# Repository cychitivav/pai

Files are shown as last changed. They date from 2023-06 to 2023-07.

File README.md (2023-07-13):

<!--
MARKDOWN IMAGES & BADGES
* https://www.markdownguide.org/basic-syntax/#reference-style-links
* https://github.com/Ileriayo/markdown-badges

EMOJIS
* https://gist.github.com/rxaviers/7360908
  
Find and replace the following text with the name of the project:
	pai
-->

<div align="center" id="readme-top">



<!-- omit in toc -->
# PAI's project
Code and documentation for a UGV that can work and be teleoperated in a field.

[**Explore the docs »**](https://cychitivav.github.io/pai)

[View Demo](https://github.com/cychitivav/pai) · [Report Bug](https://github.com/cychitivav/pai/issues) · [Request Feature](https://github.com/cychitivav/pai/issues)







</div>

<!-- TABLE OF CONTENTS -->
<!-- omit in toc -->
## :pencil:Table of contents
- [:pushpin:About The Project](#pushpinabout-the-project)
	- [Built With](#built-with)
- [:checkered\_flag:Getting Started](#checkered_flaggetting-started)
	- [Prerequisites](#prerequisites)
	- [Installation](#installation)
	- [GitHub Codespace](#github-codespace)
- [:balloon:Usage](#balloonusage)
- [:key:License](#keylicense)
- [:pencil2:Authors](#pencil2authors)
- [:tada:Acknowledgments](#tadaacknowledgments)

<!-- ABOUT THE PROJECT -->
## :pushpin:About The Project

<div align="center">
	<a href="https://cad.onshape.com/documents/2c5667e2c198d5de4bff6632/w/6e55e179f397483a4657fa47/e/d5c2a6fd63cf397246fd908f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">
		
	</a>
</div>

Welcome to the PAI ROS 1 package repository! This package contains source code and documentation for a UGV that can work in a field. This project is part of the *PAI* subject at the Universidad Nacional de Colombia.

> __Note__: This package is being developed using ROS noetic 

<!-- BADGES
https://github.com/Ileriayo/markdown-badges -->
### Built With
* 
* 
* 

<!-- GETTING STARTED -->
## :checkered_flag:Getting Started

This is an example of how you may give instructions on setting up your project locally.
	To get a local copy up and running follow these simple example steps.

### Prerequisites
In order to avoid installing ROS on your local machine, we will be using a docker image to run ROS. So, you will just need to install [Docker](https://docs.docker.com/get-docker/) in your local machine.

### Installation

1. Clone the repo
	```bash
	git clone https://github.com/cychitivav/pai.git
	```
2. Build the docker image
	```bash
	docker build -t pai:latest .
	```
3. Run the docker image
	```bash
	docker run -it \
     		   --rm \
			   -v /tmp/.X11-unix:/tmp/.X11-unix:rw \
               -v $PWD:/root/catkin_ws/src/pai \
			   --name pai \
			   pai:latest
	```
	> __Note__: If you have troubles with the display, try to run the following command before running the docker image:
	> ```bash
	> xhost +local:root
	> ```

### GitHub Codespace
Codespaces add an easy way to start contributing to this project. Some extra step are needed to run the visualization in a remote machine. You need to create a GitHub Codespace:

1. To create a Codespace, click on the following button:
   
	
2. Choose the configuration that best suits you (A high performance configuration is recommended)
3. Wait for the Codespace to be created and set up (It will appear a terminal which is running some scripts)
4. Set a password for the root user
	```bash	
	passwd
	```

From your local machine, you will need to run the following command:

```bash	
gh cs ssh -- -XY
```

> __Note__: You need to have the [GitHub CLI](https://cli.github.com/manual/installation) installed in your local machine.

Then, select the Codespace that you want to connect to and enter the password that you set before.

<!-- USAGE EXAMPLES -->
## :balloon:Usage
In order to run the package, you will need to follow the next steps from the workspace directory (by default, `~\catkin_ws`):

1. Compile packages
```bash
catkin build
```
1. Source the workspace
```bash
source devel/setup.bash
```
1. Launch the package
```bash
roslaunch pai view_robot.launch
```

<!-- ROADMAP -->
<!-- ## :roller_coaster:Roadmap

- [ ] Feature 1
- [ ] Feature 2
    - [ ] Nested Feature

> __Note__: See the [open issues](https://github.com/cychitivav/pai/issues) for a full list of proposed features (and known issues). -->

<!-- CONTRIBUTING -->
<!-- ## :busts_in_silhouette:Contributing

If you have a suggestion that would make this better, please create a pull request.

1. Create your Branch (`git checkout -b <type>/<name>`)
2. Commit your Changes (`git commit -m 'Add some AmazingFeature'`)
3. Push to the Branch (`git push origin <type>/<name>`)
4. Open a Pull Request (in the `git push` response, it appears a link to open a PR) 

The available contribution types are:
* `docs`
* `feat`
* `dev`
* `fix`

Don't forget to give the project a star! Thanks again!
 -->

<!-- LICENSE -->
## :key:License
Distributed under the MIT License. See [`LICENSE`](LICENSE) for more information.

<!-- CONTACT -->
## :pencil2:Authors
* [@cychitivav](https://github.com/cychitivav)
* [@jsduenass](https://github.com/jsduenass)
* [@juvallejom](https://github.com/juvallejom)
* [@Canborda](https://github.com/canborda)
* [@Camilo96A](https://github.com/camilo96a)
* [@jodiazro](https://github.com/jodiazro)

<!-- ACKNOWLEDGMENTS -->
## :tada:Acknowledgments

* Thanks to the [SIMA student group]() who help out supporting this project.

<div align="right">

[:arrow_double_up:back to top](#readme-top)
</div>

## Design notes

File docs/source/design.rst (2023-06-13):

.. _design:
    
Diseño conceptual
#################
Generación de conceptos a partir de análisis funcional y requerimientos
=======================================================================
Alternativas de solución
------------------------
Al momento de buscar alternativas de solución se realizó el boceto de diferentes configuraciones de ruedas, así como mecanismos de transmisión de potencia y sistemas de amortiguamiento  (ver Anexo 400-9 reporte de boceto)

Definición de subsistemas
=========================
Estructura
----------
La estructura está compuesta por placas paralelas atornilladas a los subsistemas de transmisión. De igual forma, la estructura de soporte de interfaz se atornilla a las placas paralelas. Se usa una chapa superior con una matriz de agujeros como interfaz donde se ubican los futuros posibles sensores a usar.

Transmisión y suspensión
------------------------
El sistema de transmisión consta de un eje acoplado al motor, y un elemento de transmisión de torque hacia el acople de la llanta. Este eje irá soportado sobre dos rodamientos que garantizarán la estabilidad estática de este subsistema. También se contará con un mecanismo basculante donde se podrá incorporar una amortiguador para cada una de los subsistemas de transmisión de potencia. 

Potencia eléctrica
------------------
Este sistema está compuesto por un motor eléctrico, una batería y un controlador. El motor eléctrico es el encargado de generar el torque necesario para el movimiento del vehículo. La batería es la encargada de almacenar la energía eléctrica que será suministrada al motor. El controlador es el encargado de regular la energía que es suministrada al motor, de acuerdo a las instrucciones que recibe del sistema de control y comunicación.

Control y comunicación
----------------------
Finalmente, el sistema de control y comunicación está compuesto por una Raspberry Pi, la cual es la encargada de procesar la información recibida por el módulo de comunicación inalámbrica y enviar las instrucciones al sistema de potencia eléctrica.

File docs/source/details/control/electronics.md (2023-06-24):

# Electronics 

## Raspbery pin out 

```{image} https://github.com/cychitivav/pai/assets/30636259/018453a2-3278-494c-a706-0de937c5933a
:alt: Raspberry pin out
:width: 60%
:align: center
```

### Driver left

- FAULT: 35 (GPIO 19)
- PWM2: 31 (GPIO 6) # Back left motor
- PWM1: 19 (GPIO 10) # Front left motor
- DIR2: 13 (GPIO 27)
- DIR1: 11 (GPIO 17)
- EN: 7 (GPIO 4)

### Driver right

- FAULT: 8 (GPIO 14)
- PWM2: 18 (GPIO 23) # Back right motor 
- PWM1: 22 (GPIO 25) # Front right motor
- DIR2: 24 (GPIO 8)
- DIR1: 32 (GPIO 12)
- EN: 40 (GPIO 21)

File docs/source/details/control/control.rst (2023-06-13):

Subsistema de control y comunicaciones
######################################
Selección de unidad de control
==============================
Para la unidad de control encargada de la recepción y procesamiento de datos así como las señales de mando y la transmisión de señales de pwm para el control de los drivers. (Ver anexo 400-15) Donde se tuvieron en cuenta los parámetros de Tensión de Operación, Alimentación, Consumo, Puertos Digitales	Puertos Análogos y Comunicaciones con las que contaba cada tarjeta.

.. toctree::
    electronics

Diseño de conexiones
====================
El subsistema de control y comunicación comprende a diversos elementos electrónicos de control y transmisión. A continuación se listan los componentes vinculados: 
* Raspberry Pi 4
* 2 Drivers Pololu Dual MAX14870 Motor Driver Shield for Arduino
* Regulador de Tensión de 5V a 3A
* Circuito Integrado ATtiny85-20P
* Fusibles y elementos de protección.
* Elementos de conexión : Borneras, interruptores, pines de interconexión.

El diseño electrónico generado se alimenta con la batería de 24V .El subsistema de control se divide en tres secciones independientes.

Alimentación de la tarjeta Raspberry Pi 4.
------------------------------------------
Esta sección está destinada a alimentar la tarjeta Raspberry a partir de la alimentación inicial.  Ya que la tarjeta se alimenta con una tensión de 5V  a una corriente de 3A se requiere incluir un regulador de tensión y demás elementos de protección(fusibles de 3A) para no poner en riesgo la integridad de la tarjeta.

circuito A

Sección Circuito integrado ATtiny 85-20P
----------------------------------------
circuito B

Circuito de control de motores 
------------------------------
Esta sección del montaje eléctrico cuenta con un consumo máximo de 8 amperios, a raíz del consumo de corriente individual de cada uno de los motores.
El circuito parte de una línea de alimentación de 24V y un elemento de activación (interruptor de Parada de Emergencia) el cual interrumpe el funcionamiento del vehículo sin necesidad de apagar el sistema de control en su totalidad, apagando únicamente los motores.
Esta línea alimenta los drivers los cuales controlan 2 motores cada uno. A partir de la tarjeta de control Raspberry se controlan los valores de PWM y Dirección. Ver planos

circuito C

Fabricación de PCB
==================
El diseño electrónico propuesto para el subsistema de control implica un gran número de conexiones, sin embargo no se amerita la fabricación de una Placa de Circuito Impreso de doble cara.
Uno de los factores de  diseño y fabricación de esta placa es la presencia de altas corrientes en ella. Para la capa de cobre trasera (B.Cu) se manejó un grosor estándar de 0.035mm. En función de este espesor y la cantidad de corriente que transita por las pistas se definió el ancho de las mismas generando tres clases : 

+---------------+----------------+----------------------------+-----------------------+
| Tipo de Pista | Ancho de Pista | Factor de Diseño           | Aplicaciones          |
+===============+================+============================+=======================+
| Pista A       | 0.4 mm         | Baja corriente. Caminos que| Conexiones entre el   |
|               |                | no requieren ningún tipo de| circuito integrado,   |
|               |                | limitación en corriente. Se| la tarjeta Raspberry y|
|               |                | escoge este espesor por    | los controladores.    |
|               |                | viabilidad de las          |                       |
|               |                | conexiones a raíz de un    |                       |
|               |                | proceso de iteración en el |                       |
|               |                | diseño.                    |                       |
+---------------+----------------+----------------------------+-----------------------+
| Pista B       | 1.27 mm        | Pistas con una corriente   | Conexiones de potencia| 
|               |                | admisible de 3 A.          | para la tarjeta       |
|               |                |                            | Raspberry.            |
+---------------+----------------+----------------------------+-----------------------+
| Pista C       | 2.54 mm        | Pistas con una corriente   | Alimentacion de       |
|               |                | admisible de 8 A           | Controladores y       |
|               |                |                            | motores.              |
+---------------+----------------+----------------------------+-----------------------+

A continuación se presenta una imagen del diseño final para la Placa de Circuito Impreso vinculada al sistema de control.

PCB

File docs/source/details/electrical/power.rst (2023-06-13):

Subsistema de potencia eléctrica
================================

Selección de motores
--------------------
.. toctree::
    motor

Selección de controladores de motor
-----------------------------------
Para la implementación de los motores DC seleccionados es necesario incluir un controlador de motor o Driver con el fin de modificar la señal de control adaptándola para que esta esté en la capacidad de inducir movimiento en el motor. 

Para dicha selección se tuvieron en cuenta cinco parámetros principales enumerados a continuación : 
* **Tensión o Voltaje de operación [V]:** Se seleccionan drivers cuyo voltaje de alimentación sea superior al voltaje del motor. Por generalidad, se opta por tensiones de alimentación esté entre 1,5 y 2 veces el voltaje del motor.
* **Corriente Promedio [A]:**  Parámetro relacionado con la corriente consumida por el controlador. Como criterio de selección para este parámetro ,se definió que su valor mínimo  debe ser la corriente asociada al torque máximo que puede entregar el motor (stall current).
* **Tensión de la señal de control [V]:** Valor de voltaje para la señal de salida del driver. 
* **Frecuencia de PWM [kHz]:** Frecuencia de los pulsos de la señal de control. 
* **Reversibilidad:** Se evalúa la capacidad del controlador de invertir el sentido de giro para el motor seleccionado.

Matriz de decisión para la selección de driver
^^^^^^^^^^^^^^^^^^^^^^^^^^^^^^^^^^^^^^^^^^^^^^

+------------------+----------------------+--------------------+--------------------------------+-------------------+----------------+
|                  | Tensión de operación | Corriente promedio | Tensión de la señal de control | Frecuencia de PWM | Reversibilidad |
+==================+======================+====================+================================+===================+================+
| RioRand Upgraded |                      |                    |                                |                   |                |
| DC Motor Pump    | 6-90 V               |  8-15 A            | 0-5 V                          | 15 kHz            | No             |
| Speed Controller |                      |                    |                                |                   |                |
| 6-90 V 15A       |                      |                    |                                |                   |                |
+------------------+----------------------+--------------------+--------------------------------+-------------------+----------------+
| RioRand 8-50V DC |                      |                    |                                |                   |                |
| Motor Speed      | 8-50 V               | 20-30 V            | 0-5 V                          | 12 kHz            | No             |
| Controller       |                      |                    |                                |                   |                |
| for Power Wheel  |                      |                    |                                |                   |                |
| PWM Switch       |                      |                    |                                |                   |                |
+------------------+----------------------+--------------------+--------------------------------+-------------------+----------------+
| RioRand 6V 12V   |                      |                    |                                |                   |                |
| 24V 28V 3A 80W   | 6-28 V               | 3A                 | 0-5 V                          | 10 kHz            | Si             |
| DC Motor Speed   |                      |                    |                                |                   |                |
| Controller       |                      |                    |                                |                   |                |
+------------------+----------------------+--------------------+--------------------------------+-------------------+----------------+
| Pololu Dual      |                      |                    |                                |                   |                |
| MAX14870 Motor   | 4,5 - 36 V           | 1,7 A              | 0-5V                           | 50 kHz            | Si             |
| Driver Shield    |                      |                    |                                |                   |                |
| for Arduino      |                      |                    |                                |                   |                |
+------------------+----------------------+--------------------+--------------------------------+-------------------+----------------+

Selección de batería
--------------------
Para la selección de la batería se establecieron los siguientes parámetros a tener en cuenta:

* **Voltaje de la batería [V]:** parámetro dependiente del tipo de motor seleccionado.
* **Capacidad de almacenamiento [mAh]:** 
* **Corriente entregada [mA]:** Parámetro relacionado con la capacidad de descarga [C] de la batería. 
* **Costo estimado [$]:** una estimación inicial de  300 mil pesos
* **Tamaño [mxmxm]:** Dependiente del tamaño de chasis 
* **Peso:** Búsqueda de reducción de peso
* **Densidad energética [Wh/kg]:**
* **Disponibilidad:** Facilidad de encontrar la batería en el comercio local.

Se realizó una búsqueda de los tipos de baterías existentes haciendo énfasis en encontrar las baterías que se utilizan en aplicaciones adyacentes, es decir baterías para vehículos eléctricos  como por ejemplo baterías usadas en bicicletas eléctricas.  Se obtuvieron como resultado  los siguientes tipos Plomo, Gel, Li-Ion, LiFePo4, LiPo, Ni-Mh, Ni-Cd. Sobre los cuales se descartaron las de Ni-Mh, Ni-Cd y gel debido a no cumplir la restricción de disponibilidad y no haber elementos asequibles en el mercado local.
Sobre las restantes se realizó una evaluación calificando su idoneidad en una una escala de 1 a 5 respecto a los parámetros de selección restante. 

+------------------+---------------------+------------------------+--------------------------+---------------------+
|                  | Plomo               | Li-Ion                 | LiFePo4                  | LiPo                |
+==================+=====================+========================+==========================+=====================+
| Voltaje          | 3                   | 5                      | 5                        | 4                   |
| de la batería    |                     |                        |                          |                     |
+------------------+---------------------+------------------------+--------------------------+---------------------+
| Debe tener un    | Batería a 12 voltios| El paquete modular     | Versión de batería a 12, | Versión a 21.5 o    |
| voltaje de hasta | Necesidad de comprar| permite establecer     | 24 y 48 V                | 25.7 V              |
| 24 V.            | 2 baterías para     | el voltaje por número  |                          |                     |
|                  | cumplir requisito.  | de baterías en serie   |                          |                     |
+------------------+---------------------+------------------------+--------------------------+---------------------+
| Capacidad de     | 5                   | 4                      | 4                        | 3                   |
| almacenamiento   |                     |                        |                          |                     |
+------------------+---------------------+------------------------+--------------------------+---------------------+
| Define la        | 7.5 Ah              | 7.8 Ah batería 6S3P    |                          |                     |
| autonomía del    |                     |                        |                          |                     |
| robot            |                     |                        |                          |                     |
+------------------+---------------------+------------------------+--------------------------+---------------------+
| Corriente        | 2                   | 4                      | 3                        | 3                   |
| entregada        |                     |                        |                          |                     |
+------------------+---------------------+------------------------+--------------------------+---------------------+
| Costo            | 3                   | 4                      | 3                        | 3                   |
+------------------+---------------------+------------------------+--------------------------+---------------------+
| Tamaño           | 2                   | 4                      | 2                        | 4                   |
+------------------+---------------------+------------------------+--------------------------+---------------------+
| Peso             | 2                   | 4                      | 2                        | 3                   |
+------------------+---------------------+------------------------+--------------------------+---------------------+
| Densidad         | 3                   | 3                      | 3                        | 5                   |
| energética       |                     |                        |                          |                     |
+------------------+---------------------+------------------------+--------------------------+---------------------+
| **Acumulado**    | **12**              | **28**                 | **23**                   | **26**              |
+------------------+---------------------+------------------------+--------------------------+---------------------+

Donde a partir de la evaluación se decidió escoger una batería ion litio de configuración 6S3P

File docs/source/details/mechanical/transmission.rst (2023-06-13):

Subsistema de transmisión
=========================
Selección de rodamientos
------------------------
Para llevar a cabo esta evaluación, se recopilaron los datos técnicos proporcionados por SKF y se compararon con los requisitos de carga especificados. Además, se consideraron aspectos como la capacidad de carga, las dimensiones del rodamiento, la calidad y confiabilidad del fabricante, así como la lubricación.

Resultados:
^^^^^^^^^^^

* **Capacidad de carga:** Según la información suministrada por SKF, el rodamiento 63003 tiene una capacidad de carga radial estática de 3,25 kN y una capacidad de carga radial dinámica de 6,56 kN. Dado que la carga radial en la aplicación es de 500 N, se determinó que el rodamiento seleccionado puede soportar de manera segura esta carga con un margen significativo.
* **Dimensiones:** El rodamiento 63003 SKF tiene un diámetro interior de 17 mm, un diámetro exterior de 35 mm y un ancho de 14 mm. Estas dimensiones son adecuadas para la aplicación en consideración, lo que permite un ajuste adecuado y un funcionamiento eficiente.
* **Calidad y confiabilidad:** SKF es reconocido como un fabricante líder en la industria de rodamientos, conocido por producir productos de alta calidad y confiables. Esto respalda la fiabilidad del rodamiento 63003 SKF y su capacidad para resistir condiciones exigentes en la aplicación.
* **Lubricación:** El rodamiento 63003 SKF se suministra prelubricado de fábrica con grasa de alta calidad. Esto reduce la fricción y el desgaste, y contribuye a una vida útil prolongada del rodamiento. Sin embargo, se recomienda mantener una adecuada lubricación durante la operación para garantizar un rendimiento óptimo a largo plazo.

En conclusión, con base en los resultados del análisis, se concluye que el rodamiento 63003 SKF es una elección adecuada para soportar cargas radiales de 500 N en la aplicación estudiada. Su capacidad de carga, dimensiones apropiadas, calidad y confiabilidad, respaldadas por la reputación del fabricante, lo convierten en una opción recomendada.

Diseño del eje y elementos auxiliares
-------------------------------------
El dimensionamiento del eje involucra varias iteraciones de diseño, donde se analizaron las distintas implicaciones que conllevaba cada geometría del eje. Inicialmente se optó por la geometría dispuesta en la figura del eje, donde se cuenta con 3 secciones de diámetros diferentes. La sección externa tendría un diámetro de 34.1 milímetros con el fin de encajar en la flor que acopla la llanta., mientras una sección central de mayor diámetro permitiría durante el progreso del diseño impedir el deslizamiento axial de este eje. El diámetro más interno corresponde a las dimensiones de los rodamientos seleccionados. Dentro de esta sección se maquinaría un agujero con chavetero que permitiría la transmisión de torque del motor a este eje. La dimensión de esta abertura estaría predefinida por las dimensiones del eje de salida del motor ya escogido. Por otro lado durante la primera iteración se establecieron las fuerzas que actuaban sobre el eje, que eran producidas por el resto de elementos en contacto con este(Rodamientos, acople llanta, eje del motor), las cuales también se encuentran en la siguiente figura.

eje1

Al considerar todas estas interacciones se llegó a un sistema estáticamente indeterminado que sería difícil de complementar con una ecuación de deformación, debido a las diferentes y complejas geometrías preliminares. Si se asume que el motor es totalmente soportado por la estructura externa, entonces este no ejercería una fuerza radial sobre el eje, solamente ejercería el torque, por lo que se para las siguientes iteraciones se despreciaría esta fuerza (E1). Durante el estudio de distribución de fuerzas sobre el eje se consideraron varios valores para s y L, y se observó que L afecta enormemente el momento flector que siente el eje, por lo que se opta por mantener esta distancia lo mínima posible. También se elige mantener la distancia entre los rodamientos de apoyo en aproximadamente 30 milímetros, con el fin de minimizar el momento a la vez que se deja espacio para el mecanismo basculante que va sobre la estructura auxiliar. 

Posteriormente se observó que el cambio de diámetro de 34 mm a 17 mm causaba un importante concentrador de esfuerzos, lo que hizo reconsiderar todo el diseño del eje. Es de esta manera que se decidió utilizar un diámetro único de 17 mm para todo el eje y de esta manera evitar los concentradores de esfuerzos por cambios abruptos de sección, para acoplar la flor de la llanta al eje se opta por usar una camisa auxiliar que permita encajar el eje y la flor de la llanta a su vez que mantiene la transición centrada. Debido a la sección única, se decidió utilizar anillos seeger para evitar el deslizamiento axial del eje. Estos anillos se situarían en unas ranuras que van en el espacio entre los dos rodamientos de apoyo. Además para transmitir el torque a la llanta se opta por usar un pasador que atraviesa la flor, la camisa y el eje como tal, por lo que se hace necesario maquinar en el eje un agujero transversal donde vaya alojado este pasador de transmisión. Es así que se llega al nuevo y definitivo diseño del eje, que se puede observar en la siguiente figura. 

eje1

Para verificar el correcto diseño de este eje se lleva a cabo un detallado análisis que permite establecer el factor de seguridad a fatiga del eje junto a los componentes auxiliares de este (Camisa y pasador). Dicho análisis puede verse en el anexo “Diseño de elementos de transmisión de potencia”. En dicho análisis se observó que se puede optimizar el factor de seguridad en función del diámetro del pasador. De este análisis se obtuvo un factor de seguridad mínimo y óptimo de aproximadamente 1.8, que corresponde a la fatiga por flexión del pasador. Ya con dicho factor se dan por establecidas todas las dimensiones del eje, camisa y pasador.

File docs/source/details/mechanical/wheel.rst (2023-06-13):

Selección de las ruedas
#######################

En el proceso de selección de las ruedas para nuestro vehículo teleoperado, consideramos diferentes aspectos para encontrar la mejor opción. Nuestro enfoque principal fue la aplicación específica del vehículo y la disponibilidad de las ruedas en el mercado.

Inicialmente, consideramos utilizar ruedas de cuatrimoto con un diámetro de rin de 6 pulgadas. Específicamente, evaluamos las ruedas *Hakuba* que presentaban un labrado de aproximadamente 1 cm, lo cual las hacía adecuadas para enfrentar los desafíos del terreno en el que operaría el vehículo.

Ruedas costosas

Sin embargo, al evaluar los costos asociados y los requisitos de diseño adicionales, decidimos descartar esta opción. El costo de estas ruedas de cuatrimoto ascendía a 1 millón de pesos, sin contar el gasto adicional de diseñar un acople para unirlas al motor del vehículo.

Posteriormente, nos dirigimos al mercado de ruedas y rodachinas en el sector de Ricaurte para buscar alternativas más económicas. Allí encontramos unas ruedas de 10 pulgadas de diámetro que incluían el rin y el acople necesario, a un costo de 50 mil pesos. Estas ruedas estaban diseñadas específicamente para plataformas de carga de hasta 200 libras, lo cual las convertía en una opción ideal para nuestro vehículo teleoperado de muestreo de suelos. Además, si el labrado no fuese suficiente para enfrentar el terreno, podríamos cambiar la llanta por una de mayor agarre, sin necesidad de cambiar el rin o el acople, esto claro, con consentimiento del cliente.

Ruedas económicas

La selección de las ruedas de 10 pulgadas nos brindó una solución más rentable, ya que cumplía con nuestros requisitos de tracción y estabilidad a un precio mucho más accesible. Además, el hecho de que estas ruedas ya incluyeran el acople necesario simplificó el proceso de integración en el vehículo, ahorrando tiempo y esfuerzo en el diseño y fabricación de un acople adicional.

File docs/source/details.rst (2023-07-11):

.. _detail:

Generación detallada del producto
#################################
Basándonos en la experiencia de expertos y diversas fuentes consultadas, se ha determinado que el diseño de cualquier vehículo debe realizarse de las ruedas hacia arriba. Esto se debe a que los componentes ubicados en la parte inferior del vehículo definen características y requisitos para los componentes superiores.

El diseño del vehículo teleoperado se inicia centrándose en las ruedas, ya que desempeñan un papel fundamental al soportar la carga, proporcionar tracción y determinar la capacidad de movimiento en el terreno. 

A medida que avanzamos en el proceso de diseño, se analizaron y definieron cuatro subsistemas principales: estructural, transmisión, potencia eléctrica y control y comunicaciones. Esto debido a que a pesar que el vehículo cuenta con cuatro ruedas, el sistema de tracción se va a comportar como un vehículo diferencial, es decir, que las ruedas del lado izquierdo y derecho se moverán de forma independiente.

.. toctree::
    :maxdepth: 2

    details/mechanical/wheel
    details/mechanical/structural
    details/mechanical/transmission
    details/electrical/power
    details/control/control
    details/control/electronics
    details/control/software_setup

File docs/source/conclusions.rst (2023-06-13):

Conclusiones y trabajo futuro
#############################
Conclusiones
============
* El prototipo desarrollado comprende una primera aproximación a la automatización de muestreo de suelos. Si bien aún se requiere de un operario que manipule el vehículo, el recorrido de este permitirá la captura de datos georreferenciados con una resolución superior a la obtenida por las técnicas tradicionales y menor tiempo requerido en campo.
* Si bien el prototipo puede no funcionar bien en algunos terrenos con pendiente o con tamaño de agregado demasiado grande, en ambientes controlados su desempeño ha sido sobresaliente.
* El diseño conceptual depende de la disponibilidad comercial de algunas piezas, esto facilita su mantenimiento y reparación en caso de ser necesario reemplazar componentes dañados o desgastados.
* El presupuesto ajustado limitó la adquisición de algunos componentes de mayor calidad o precisión que posiblemente habrían resultado en un incremento en el desempeño del prototipo final.

Trabajo futuro
==============

Autonomía del robot
-------------------
El alcance del presente proyecto limitó el prototipo a ser teleoperado, de manera que el sistema de control funciona en lazo abierto y la única realimentación de la localización del vehículo es la observación directa del operario. Se espera a futuro seguir trabajando dentro del semillero SIMA en la implementación de sensores que permitan al robot solucionar el problema de navegación y generar trayectorias de forma independiente.

Suspensión
----------
Si bien el diseño de detalle presenta un sistema de amortiguamiento, este no pudo ser implementado en la construcción del prototipo debido a problemas de disponibilidad de los componentes. Se espera en un futuro adquirir los resortes que cumplan con las especificaciones calculadas e instalarlos en el prototipo.

Captura de datos
----------------
El subsistema de captura de datos georreferenciados no estaba contemplado en el presente proyecto, sin embargo comprende la aplicación real del vehículo desarrollado. El objetivo del semillero es proponer un nuevo proyecto para diseñar y/o adecuar sensores que permitan la medición de variables físicas del suelo e implementar (en lo posible en el mismo controlador) un software que almacene estas mediciones para futuro procesamiento.

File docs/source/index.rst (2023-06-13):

Vehículo de Muestreo
####################

Este informe presenta el diseño y desarrollo de un vehículo de muestreo en aplicaciones agrícolas, diseñado para facilitar la recolección eficiente y precisa de muestras de suelo en áreas no perturbadas. El vehículo fue concebido como parte de un proyecto de la materia Proyecto Aplicado de Ingeniería en la Universidad Nacional de Colombia. El proyecto fue desarrollado por un equipo de 7 estudiantes de ingeniería mecánica y mecatrónica, bajo la supervisión de un profesor de la facultad de ingeniería.

En el presente informe, se describirán los pasos clave seguidos en el proceso de diseño y construcción del vehículo, así como las pruebas y validaciones realizadas para evaluar su desempeño y funcionalidad. También se incluirán los detalles técnicos relevantes, como las especificaciones del vehículo, los componentes utilizados y los procedimientos de operación.

Esperamos que este informe sirva como una guía útil para aquellos interesados en el diseño y construcción de vehículos similares, y que fomente futuras investigaciones y desarrollos en este campo de estudio. Agradecemos cualquier comentario o sugerencia que pueda contribuir a mejorar el diseño y funcionalidad del vehículo en futuras iteraciones.

.. toctree::
   :maxdepth: 3
   :caption: Tabla de contenido
   :numbered:

   problem
   metodology
   design
   details
   verification
   manufacturing
   validation
   conclusions

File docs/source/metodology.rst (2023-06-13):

Metodología del proyecto
########################
Para el presente proyecto se optó por una metodología en cascada ya que sus etapas debían desarrollarse de manera secuencial y el alcance está limitado a una sola iteración (tanto por recursos económicos como temporales), que consiste en la construcción de un primer prototipo como producto final. Las subsecciones siguientes describen las etapas seguidas y las actividades para cada una.

Etapa de análisis de requisitos
===============================
En esta etapa se recopilaron los requisitos del proyecto con base en las necesidades del cliente y a partir de investigación y asesoría por parte de expertos. Las principales actividades desarrolladas se describen a continuación.

Investigación del estado del arte
---------------------------------
Se realizó una investigación detallada de los diferentes robots móviles con aplicaciones en agricultura (como se ha descrito brevemente en la sección :ref:`art`) desde dos perspectivas; modelos que se consiguen comercialmente y prototipos desarrollados en un ambiente más académico e investigativo. Esta contextualización permitió comprender las especificaciones y requerimientos de ingeniería, y una vez comprendidos los parámetros se comenzaron a proponer ideas de diseño a partir de diferentes técnicas de trabajo grupal como lluvia de ideas.

Asesoría de expertos
--------------------
Con el fin de comprender a profundidad el proceso de diseño y los parámetros requeridos para la construcción de un robot con las características solicitadas, se buscó asesoría en diferentes personas con conocimiento y experiencia en el área de la robótica móvil y de la tecnificación de la agricultura. El ingeniero Carlos Velázquez (AmiTech), a partir de su experiencia trabajando con robots móviles, dio recomendaciones sobre diferentes modelos que se podían usar como base y tipos de transmisión, también hizo comentarios sobre el nivel de autonomía que puede tener el robot móvil en relación con su complejidad, y sobre alternativas de alimentación para el sistema eléctrico. Por otra parte, el ingeniero Luis David Ordoñez es docente del curso de Electrotecnia impartido para el programa de Ingeniería Agrícola y ha trabajado con UAV y UGV en labores agrícolas, y su asesoría se enfocó principalmente en cómo solucionar el problema de tracción y navegación del vehículo junto con la adquisición de datos georreferenciados (subsistema fuera del alcance del presente proyecto). Finalmente, el ingeniero Felipe González ex docente de la asignatura de Robótica, realizó aportes sobre el modelo cinemático para un robot móvil tipo diferencial.

Reuniones con cliente
---------------------
Otra actividad recurrente en esta etapa fue una serie de reuniones con el cliente y varios miembros del semillero SIMA con el fin de comprender y detallar las necesidades del problema y además obtener retroalimentación sobre las ideas y propuestas que se iban presentando. Los temas discutidos se detallan en las actas.

Etapa de diseño
===============
Una vez establecidos los requisitos se procedió al diseño conceptual y de detalle del producto. Para esta etapa se utilizó la plataforma OnShape que permite el modelado CAD con control de versiones de manera que se pudieran visualizar y probar múltiples conceptos sin afectar el diseño principal. Este diseño comenzó a partir de los bocetos generados en la lluvia de ideas y modelos base obtenidos en la etapa previa del proyecto, posteriormente se definieron los subsistemas y se inició con el diseño de detalle aplicando los conceptos de ingeniería adquiridos a lo largo de la formación académica (la profundización de este proceso se describe en las secciones :ref:`design` y :ref:`detail`). Esta etapa describe un proceso cíclico dentro del diseño, ya que a partir de cálculos previos se diseñan piezas y se seleccionan componentes que posteriormente son simulados o verificados de manera que cumplan teóricamente con los requerimientos, en caso de falla se debe volver a diseñar o cambiar la pieza y retornar a la verificación hasta que todas las partes hayan sido aprobadas.

Etapa de implementación
=======================
Esta etapa comprende la construcción física del vehículo. Para esto se dividió en tres actividades principales; la fabricación de las piezas diseñadas y la adquisición de piezas estandarizadas debían llevarse a cabo de forma paralela, teniendo en cuenta los tiempos de fabricación y de envío según correspondiera, para posteriormente iniciar con el ensamble y puesta a punto del prototipo. Para esta etapa se contó con empresas proveedoras de material industrial, diferentes negocios de mecanizado y corte láser en la ciudad de Bogotá y además se dispuso del Laboratorio de Mecanización en el edificio de Ingeniería Agrícola de la Universidad Nacional de Colombia sede Bogotá para todo el proceso de ensamblado. Más detalle de esta etapa se describe en la sección :ref:`assembly`.

Etapa de pruebas y validación
=============================
Una vez finalizado el ensamble del prototipo, este se someterá a una serie de pruebas que comprueben el correcto funcionamiento de cada uno de los subsistemas que lo comprenden. Estas pruebas deben ser ejecutadas en ambiente controlado y se deberán realizar mediciones de las variables que confirmen que el modelo cumple con los requerimientos de diseño definidos. Las validaciones a realizar se describen en el anexo de protocolos de validación.

Etapa de mantenimiento y soporte
================================
Una vez validado el prototipo al cliente, se hará la entrega formal donde se indiquen las instrucciones de uso, recomendaciones y futuras mejoras, dando así como finalizada la vinculación formal del contrato social. Sin embargo, se ha extendido la invitación a los integrantes del equipo de trabajo para continuar con el proyecto desde el semillero.

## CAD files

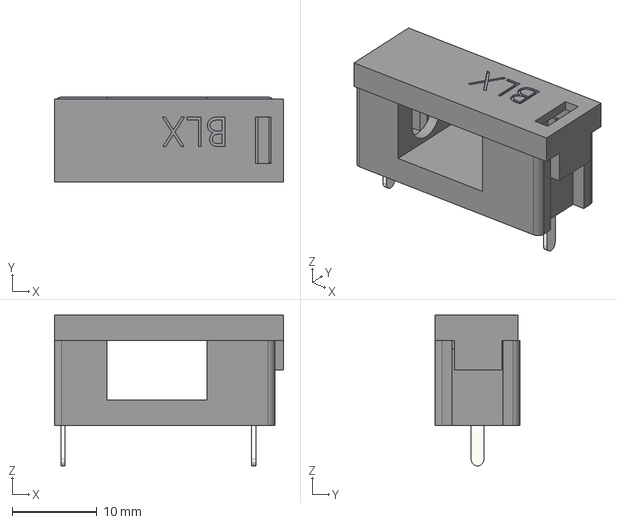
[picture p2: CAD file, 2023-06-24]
kicad/model/Fuse Holder.step
27.0 x 10.0 x 17.8 mm

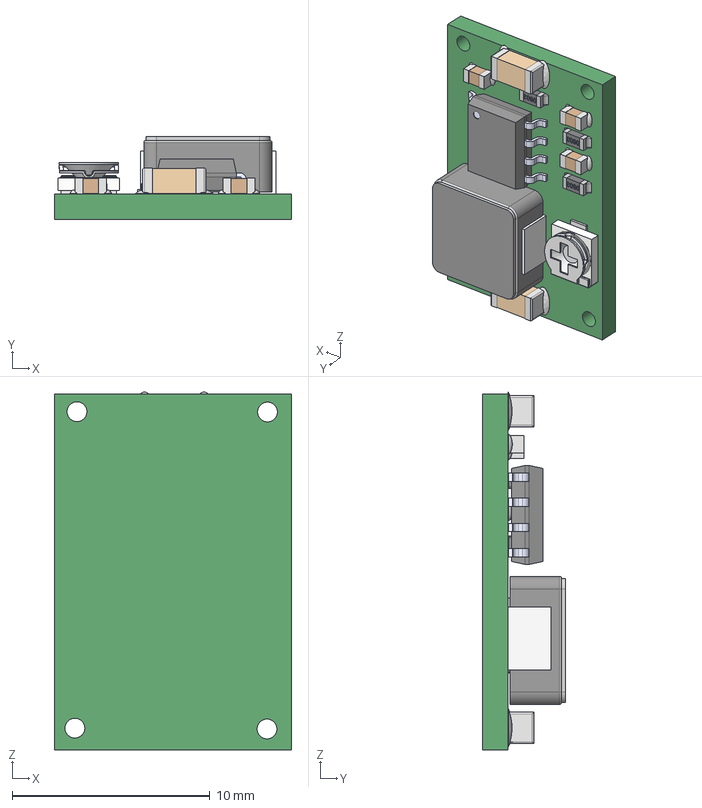
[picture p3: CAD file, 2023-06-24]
kicad/model/dsn-mini-360.step
12.0 x 4.20 x 18.1 mm
User Library-SOIC-8 - TEK
Resistor 0603 x 3
CAPC0603 x 3
CAPC1206 x 2
EVM-3E

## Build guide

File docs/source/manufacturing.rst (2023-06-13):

.. _assembly:

Fabricación y ensamble
######################

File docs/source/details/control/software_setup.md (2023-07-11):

# Raspberry set up

## Install OS
This project is using Ubuntu 20.04 as the base OS. Use the official ubuntu guide and follow step by step installation process. [^os-install]

 > __Note:__ Ubuntu Desktop 2020 is not available in the rpi-imager so Ubuntu Server 2020 is the one used. And the following command is needed to download the necessary package to configure the desktop version.
 > ```
 > sudo apt update
 > sudo apt install ubuntu-desktop
 > ```

## Set up ROS
Follow the ROS installation guide [^ros-install] to install __ROS noetic__.

## Install pigpio lib
Install the pigpio library with the following commands [^pigpio-install].

```bash
apt install unzip
wget https://github.com/joan2937/pigpio/archive/master.zip
unzip master.zip
cd pigpio-master
make
sudo make install
sudo rm -rf master.zip pigpio-master
```

## Get project 
This project is configured as a ROS package. Clone the repo inside your workspace

```bash
mkdir -p ~/catkin_ws/src
cd ~/catkin_ws/src
git clone https://github.com/cychitivav/pai
```

## Build the ROS package

```bash
cd ~/catkin_ws
catkin build
source devel/setup.bash
```
## Run robot

```
roslaunch pai run_robot.launch
```

```
rostopic pub  -r 0.5 /front_right_wheel_ctrl/command std_msgs/Float64 "64.0"
```

```
rostopic pub -r 0.5 /cmd_vel geometry_msgs/Twist "linear:
  x: 1.0
  y: 0.0
  z: 0.0
angular:
  x: 0.0
  y: 0.0
  z: 0.1"
```

For further configuration check out the Miscellaneous section.

## Slow boot time
At start up the `systemd-networkd-wait-online.service` waits for a network to be connected. Which makes the the start up time really long if no network is connected. You change the configuration of the service in order to reduce the wait time. Find the line  that starts with `ExecStart=[PATH]`inside the  `systemd-networkd-wait-online.service` and add the  parameter `--timeout=10`

```
sudo systemctl disable NetworkManager-wait-online.service
sudo nano  systemd-networkd-wait-online.service
#  ExecStart=/lib/systemd/systemd-networkd-wait-online --timeout=10
```

## Autostart pigpio deamon at boot
If `pigpio` is installed from the source code, the deamon needs to be started manually, due to the fact that the installation process does not create a service. To start the deamon at boot, create a service configuration file in the following path `/etc/systemd/system/pigpiod.service.d/public.conf` and add the following lines.

```conf
[Service]
ExecStart=
ExecStart=/usr/local/bin/pigpiod
```

Then, create the service file `/lib/systemd/system/pigpiod.service` and add the following lines.

```conf
[Unit]
Description=Daemon required to control GPIO pins via pigpio
[Service]
ExecStart=/usr/local/bin/pigpiod
ExecStop=/bin/systemctl kill -s SIGKILL pigpiod
Type=forking
[Install]
WantedBy=multi-user.target
```

And finally, enable and start the service.
```bash
sudo systemctl deamon-reload
sudo systemctl enable pigpiod
sudo systemctl start pigpiod
```

## I²C setup
In some cases the I²C bus is not enabled by default. To check if the I²C bus is enabled, run the following command.

```bash
ls /dev/i2c*
```

If the command does not return any result, the I²C bus is not enabled. To enable the I²C bus, run the following commands

1. Open the file `/etc/modules` and add the following lines at the end of the file.

  ```conf
  i2c-dev
  i2c-bcm2708
  ```
1. Open the file `/boot/config.txt` and add the following lines at the end of the file.

  ```conf
  dtparam=i2c_arm=on
  dtparam=i2c1=on
  ```
1. Reboot the system.

Finally, check if the I²C bus is enabled by running the following command.

```bash
sudo i2cdetect -y 1
```

> __Note__: Install the `i2c-tools` package from `apt` to use the `i2cdetect` command.

<details>
  <summary><h2>Miscellaneous configuration </h2></summary>
  <p>ssh remote.</p>
  <p>development environment (install vscode and list of vscode extensions).</p>
  <p>add raspbian apt archive.</p>
  <p>configure vnc server.</p>
  
</details> 

## References

[^os-install]:[How to install Ubuntu Desktop on Raspberry Pi](https://ubuntu.com/tutorials/how-to-install-ubuntu-desktop-on-raspberry-pi-4#1-overview)

[^ros-install]:[ROS install](http://wiki.ros.org/noetic/Installation/Ubuntu)

[^pigpio-install]:[pigpio installation guide](https://abyz.me.uk/rpi/pigpio/download.html)

[^vnc-server-install]:[install and configure vnc on ubuntu 20-04](https://www.digitalocean.com/community/tutorials/how-to-install-and-configure-vnc-on-ubuntu-20-04)

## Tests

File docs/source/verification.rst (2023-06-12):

Proceso de verificación
#######################

Caracterización de motor
========================

Corriente de consumo sin carga
------------------------------

Corriente de bloqueo
--------------------

.. note::
   [Anexar enlace a video de prueba]

Control de velocidad de rueda
=============================

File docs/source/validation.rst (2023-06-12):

Proceso de validación
#####################

.. note::
    Anexar el protocolo de validación

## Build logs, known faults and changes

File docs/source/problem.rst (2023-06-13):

Planteamiento del problema y especificaciones
#############################################
Marco teórico
=============
Muestreo de suelos
------------------
El muestreo de suelos es la actividad de recolección de muestras representativas de suelo mediante distintas técnicas, con el fin de proporcionar información clave sobre sus propiedades físicas, químicas y biológicas. El muestreo busca determinar la variabilidad espacial y temporal de las propiedades del suelo, útiles para evaluar la calidad del suelo y diagnosticar problemas relacionados. Parte fundamental del proceso consiste en el diseño de experimento, selección del tamaño de la muestra y de los métodos de muestreo; para esto se debe determinar el sensor a utilizar (de acuerdo a la variable que se desea medir), así como seleccionar la unidad de muestreo y el recorrido que puede ser aleatorio o sistemático (comúnmente zigzag o cuadrícula).

Robótica móvil en la agricultura
--------------------------------
Un robot móvil es un sistema robótico capaz de desplazarse en distintos entornos y que cuenta con capacidades que le permiten ejecutar tareas complejas en un espacio amplio, ya sea de forma autónoma o controlado por un operador humano. En la agricultura los robots móviles de uso más común son los vehículos aéreos no tripulados UAV (unmanned aerial vehicle) y los vehículos terrestres no tripulados o UGV (unmanned ground vehicle) que se caracterizan por operar estando en contacto con el suelo; generalmente los primeros son utilizados para labores de monitoreo y supervisión, mientras que los segundos son para tareas de aplicación o interacción directa con los cultivos. La finalidad de la utilización de los robots móviles en la agricultura es automatizar algunos procesos agrícolas para que sean llevados a cabo de manera más eficiente y precisa en comparación con los métodos tradicionales, además de reemplazar la intervención humana en labores que pueden ser perjudiciales para su salud (como el caso de la aplicación de químicos).

Planteamiento del problema
==========================
El Semillero de Investigación de Maquinaria Agrícola SIMA está buscando ofrecer el servicio de muestreo y mapeo de propiedades físicas del suelo de manera teleoperada y que sea asequible a pequeños productores agrícolas. Para esto requieren de un mecanismo capaz de recorrer terreno de suelo desnudo, que sea fácil de transportar, y que cuente con una plataforma donde instalar los distintos sensores requeridos. Para la primera etapa, el semillero limitará la implementación de la solución a parcelas pertenecientes a la sabana de Bogotá (terreno plano).

Objetivos
=========
Objetivo general
----------------
Desarrollar un prototipo de vehículo terrestre no tripulado (UGV) capaz de recorrer un terreno plano sin labrar, siguiendo una trayectoria definida de forma teleoperada y que cuente con una interfaz o plataforma para instalar sensores y dispositivos para medición de propiedades físicas del suelo.

Objetivos específicos
---------------------
* Diseñar y simular el UGV para diferentes configuraciones de carga (sensores).
* Diseñar e implementar un sistema de control que permita al vehículo seguir trayectorias (en lazo abierto).
* Validar el prototipo en un lote perteneciente a la Universidad Nacional de Colombia previamente adecuado.
* Elaborar informe de trabajo y manual de uso.

Estudio preliminar de factibilidad
==================================
.. _art:

Estado del arte
---------------
Empresas internacionales de soluciones tecnológicas en la agricultura como Blue River Technology o Ecorobotix, han desarrollado y comercializan dispositivos inteligentes para aplicaciones en cultivos, sin embargo estos vehículos no son autónomos y se requiere de un tractor para moverlos en el terreno de interés. Otras empresas como Robotnik, se dedican a comercializar robots móviles y manipuladores móviles de propósito general, de manera que pueden ser fácilmente adaptables para tareas agrícolas. Los productos encontrados en el mercado se caracterizan por ser vehículos de gran tamaño enfocados a cultivos de gran extensión, además, la representación de las marcas en Colombia es casi nula lo que complica el servicio técnico.

A nivel investigativo, se han encontrado algunos trabajos universitarios similares como el “Prototipo de robot móvil autónomo para caracterizar suelos de cultivo” desarrollado en el Instituto Politécnico Nacional de México, o el “Agrobot CERES” desarrollado por la Universidad Militar Nueva Granada en conjunto con la Universidad Nacional de Colombia. Estos modelos presentan un primer acercamiento al producto que se pretende desarrollar y han sido usados como guía en la etapa de diseño, sin embargo, no son una solución final para el problema abordado en el presente trabajo.

Manufactura
-----------
Como primera medida se consideran los servicios de manufactura que ofrecen los diferentes laboratorios de la Universidad Nacional de Colombia. Posteriormente se realizó una investigación respecto a los procesos de manufactura disponibles comercialmente en la ciudad de Bogotá que sean asequibles en cuanto a costos, y se elaboró una lista de proveedores que permitieran abastecer los componentes necesarios (ver anexo 400-8). En esta etapa se encontró que los procesos a los que se tiene acceso son operaciones de metalmecánica y maquinado convencional, doblado de perfiles, soldadura y fabricación de PCB  de agujero pasante. Para las labores de corte, taladrado, esmerilado y soldadura se cuenta con los equipos necesarios en el Laboratorio de Mecanización del departamento de Ingeniería Agrícola, laboratorio que pertenece al semillero (cliente).

Presupuesto
-----------
Como se contempla en el contrato social, el presupuesto del que se dispone es de máximo 5'000.000 COP, que serán retornados en su totalidad por el cliente previa presentación de las facturas de los componentes o procesos de manufactura contratados, siempre con un compromiso por parte de los integrantes del equipo de optimizar los recursos.

Desarrollo y análisis de requerimientos
=======================================
* **Portabilidad y desmontabilidad:** El mecanismo no deberá sobrepasar los 60 Kg de peso total, y debe ser parcialmente desarmable, de manera que su transporte y posterior reensamblaje sea cómodo y rápido.
* **Carga útil:** El producto deberá ser capaz de soportar en su plataforma una carga de hasta 6 Kg correspondiente a algún sensor.
* **Capacidad de recorrido:** La autonomía del vehículo debe permitirle recorrer un lote de al menos un cuarto de fanegada en una carga completa para garantizar la eficiencia del proceso de muestreo.
* **Resolución espacial:** El subsistema de adquisición de datos debe ser capaz de almacenar datos con una resolución espacial mínima de al menos 50 cm para garantizar que la precisión de la variable sensada sea mejor que la obtenida por métodos tradicionales.
* **Limitaciones geográficas:** Este primer prototipo estará limitado a funcionar en parcelas pertenecientes a terrenos de la Universidad Nacional de Colombia sede Bogotá, los cuales se caracterizan por ser terreno plano, de corta extensión y de suelo desnudo.

Desarrollo y análisis de especificaciones de ingeniería
=======================================================

Valores priorizados
-------------------
La tabla presenta los requerimientos de ingeniería que han sido tomados en cuenta para la etapa de diseño, así como las respectivas métricas que se deben cumplir en el prototipo final. La tabla está organizada en orden de prioridad, de manera que un parámetro ubicado en una fila superior tendrá prioridad sobre otro ubicado en una fila inferior.

+----------+-------------------------------------+----------------+-----------+-----------------------------------------------------+
| Código   | Requerimiento                       | Valor y unidad | Objetivo  | Criterio de evaluación                              |
+==========+=====================================+================+===========+=====================================================+
| 2.6.1.1. | Carga útil                          | :math:`5\ kg`  | maximizar | Pesar la carga adicional a acoplar en el vehículo y |
|          |                                     |                |           | ponerlo en funcionamiento con esta.                 |
+----------+-------------------------------------+----------------+-----------+-----------------------------------------------------+
| 2.6.1.2. | Peso                                | 60 Kg          | minimizar | Pesar el robot completamente ensamblado y ponerlo en|
|          |                                     |                |           | funcionamiento.                                     |
+----------+-------------------------------------+----------------+-----------+-----------------------------------------------------+
| 2.6.1.3. | Volumen                             | 1 m^3          | minimizar | Medir los valores máximos de alto, largo y ancho del|
|          |                                     |                |           | del robot completamente ensamblado y calcular su    |
|          |                                     |                |           | volumen.                                            |
+----------+-------------------------------------+----------------+-----------+-----------------------------------------------------+
| 2.6.1.4. | Velocidad de crucero                | 7 Km/h         | maximizar | Definir una trayectoria de distancia conocida,      |
|          |                                     |                |           | cronometrar el tiempo de recorrido y con estos datos|
|          |                                     |                |           | calcular su velocidad media.                        |
+----------+-------------------------------------+----------------+-----------+-----------------------------------------------------+
| 2.6.1.5. | Distancia del suelo a la plataforma | 50 cm          | minimizar | Medir la distancia entre el suelo y la carga        |
|          |                                     |                |           | acoplada en la plataforma/interfaz.                 |
+----------+-------------------------------------+----------------+-----------+-----------------------------------------------------+
| 2.6.1.6. | Duración de un ciclo de carga       | 30 minutos     | maximizar | Cronometrar el tiempo de funcionamiento a velocidad |
|          |                                     |                |           | crucero hasta que se descargue la batería.          |
+----------+-------------------------------------+----------------+-----------+-----------------------------------------------------+
| 2.6.1.7. | Radio de giro                       | 50 cm          | minimizar | Someter al robot a movimiento circular uniforme con |
|          |                                     |                |           | diferentes radios sin que pierda el equilibrio.     |
+----------+-------------------------------------+----------------+-----------+-----------------------------------------------------+
| 2.6.1.8. | Tiempo de ensamble                  | 30 minutos     | minimizar | Cronometrar el tiempo que se tarda un operario en   |
|          |                                     |                |           | ensamblar y poner en funcionamiento el robot.       |
+----------+-------------------------------------+----------------+-----------+-----------------------------------------------------+
| 2.6.1.9. | Distancia de teleoperación          | 10 m           | maximizar | Mover el robot de manera que se aleje del centro de |
|          |                                     |                |           | mando y medir la distancia entre estos cuando se    |
|          |                                     |                |           | pierda la conexión.                                 |
+----------+-------------------------------------+----------------+-----------+-----------------------------------------------------+

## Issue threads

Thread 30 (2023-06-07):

Bug: Docker launch sim

jsduenass, 2023-06-07:
when running `roslaunch pai sim.launch` in the Docker the launch fail

```
[ERROR] [1686156460.241993689, 1.435000000]: Exception thrown while initializing controller 'right_front_ctrl'.
Could not find resource 'right_front_joint' in 'hardware_interface::VelocityJointInterface'.
```

I thought it might be related with missing ROS depedencies in however even after installing all the dependencies in https://github.com/cychitivav/pai/blob/951ca9c63c6fe73660dc87310d84bdb785153710/Dockerfile. The problem still persisted.

cychitivav, 2023-06-07:
Could you please write the whole output log?

cychitivav, 2023-06-07:
I think I found the errors. It is because joint names are defined as `<left/right>-<back/front>` and in config/controller.yaml are defined as `<back/front>-<left/right>`.

Closed 2023-06-10.

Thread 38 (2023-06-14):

Motor fail case

jsduenass, 2023-06-14:
When testing the drivers with the motors. A fail case scenario was found when running in reverse and then changing the speed to zero.

We think this might be do to inside the implementation it does the change of direction before the change of speed so when running at -50  and then send the 0 speed. It transitions from -50 to 50 to 0.

I think it would be a good idea to create a protection mechanism to avoid this fail case.

cychitivav, 2023-06-18:
Turns out the motors draw a higher (16 A max) current that the one estimated. So, we had to change these drivers for ones with a higher max current (BTS7960).

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

Closed 2023-06-18.

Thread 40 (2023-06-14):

Initialize all GPIO pins in LOW

cychitivav, 2023-06-14:
I tested the code on the raspberry and found that when I don't set all the GPIO pins to LOW, the code fails.

When I put the motors in reverse, it sends both signals(forward and reverse) and measuring with the multimeter, I found that there is a 0.5 volt offset that is only eliminated by setting all the pins to LOW.

In conclusion, we need to find a way to start `pigpiod` automatically and set this GPIO pins to LOW.

jsduenass, 2023-06-18:
This issue was caused by an error in the electronic connections.

Closed 2023-06-18.

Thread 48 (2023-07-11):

README review

jsduenass, 2023-07-11:
Hey @cychitivav after re-reading the README I think there are some things we can work on

- [ ] view demo: Create and link a demo video of the working prototype.
- [ ] Package name: we have pai as temporary name for the project I think it is time we choose a more descriptive name.
- [x] Build with tags: Add raspberry pi and kicad tags in the build with section
- [ ] Getting starded section: I think this could be moved to the documentation in the web page. (Restructure the web page documentation would be other task to work on)
- [ ] Roadmap: define if there are any new development goals you want the project to have
- [x] Autors: add missing particpants
- [x] Aknowledgement: recognize the SIMA group for the financial support of the project.

Closed 2023-07-13.

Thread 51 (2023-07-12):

configure devcontainer to be used in codespaces

jsduenass, 2023-07-12:
We have a dockerfile and a devcontainer as tools that testing easier without the need of a raspbery pi:
I would like to configure the devcontainer to make it easy to use github codespaces.

Currently there is an issue where the code is being mounted on the `/workspace` folder instead of the `root/catkin_ws/src/pai`

I'll add here relevante resource and see if I can fix it

jsduenass, 2023-07-12:
https://github.com/orgs/community/discussions/15506

Here people are having the same issue and they offer a workaround.

jsduenass, 2023-07-12:
> Finally, if you created the codespace from a repository, the entire history of the repository is copied down with a full clone. If you created the codespace from a template, the full history of the template repository is not preserved; instead, unless you are using the blank template, you will start with an initial commit for the contents of the template repository.

https://docs.github.com/en/codespaces/getting-started/deep-dive#step-4-post-creation-setup

jsduenass, 2023-07-13:
@cychitivav  a tutorial to setting up GUI applications with gh cli, ssh and  X11

```
gh cs ssh -- -XY
```

https://babyprogrammer.com/blog/running-gui-code-applications-in-github-codespaces-on-windows/

jsduenass, 2023-07-13:
closed by #52

Closed 2023-07-13.

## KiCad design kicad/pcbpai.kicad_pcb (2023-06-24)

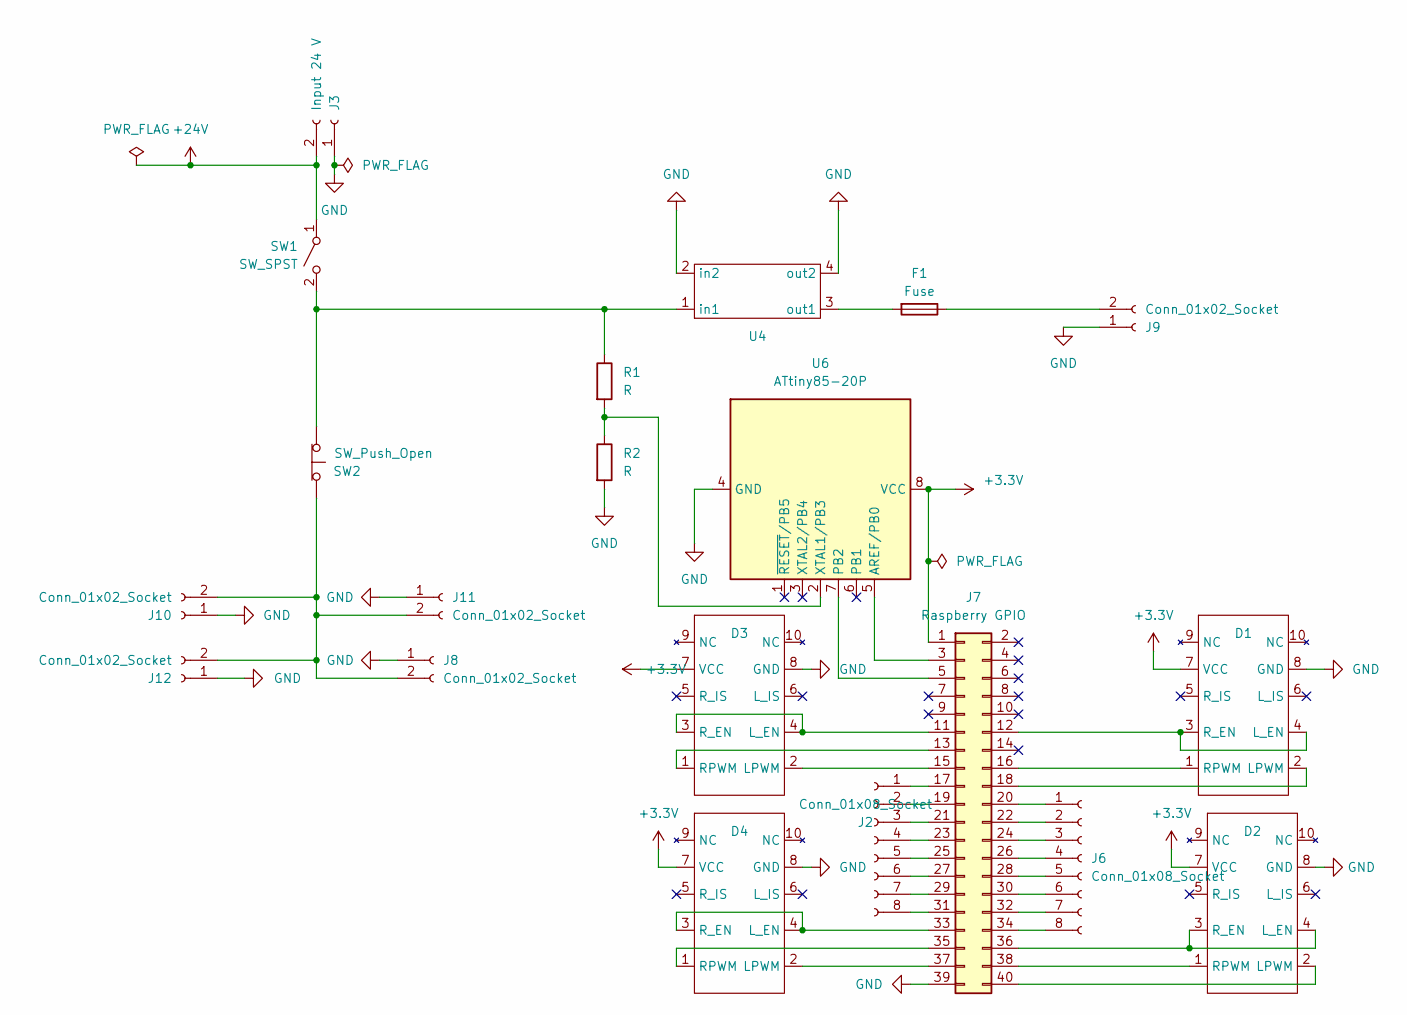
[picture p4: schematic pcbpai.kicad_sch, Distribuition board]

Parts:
D1, D2, D3, D4: IDC-Header_2x05_P2.54mm_Vertical
F1: Fuse; fuse
J2, J6: Conn_01x08_Socket; PinSocket_1x08_P2.54mm_Vertical
J3: Input 24 V; AMASS_XT60-M_1x02_P7.20mm_Vertical
J7: Raspberry GPIO; IDC-Header_2x20_P2.54mm_Vertical
J8, J10, J11, J12: Conn_01x02_Socket; PhoenixContact_MSTBA_2,5_2-G_1x02_P5.00mm_Horizontal
J9: Conn_01x02_Socket; TerminalBlock_Phoenix_PT-1,5-2-5.0-H_1x02_P5.00mm_Horizontal
R1, R2: R; R_Axial_DIN0207_L6.3mm_D2.5mm_P7.62mm_Horizontal
SW1: SW_SPST; PhoenixContact_MSTBA_2,5_2-G_1x02_P5.00mm_Horizontal
SW2: SW_Push_Open; PhoenixContact_MSTBA_2,5_2-G_1x02_P5.00mm_Horizontal
U4: regulator
U6: ATtiny85-20P; DIP-8_W7.62mm

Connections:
+3.3V: D1.7 (VCC), D2.7 (VCC), D3.7 (VCC), D4.7 (VCC), J7.1, U6.8 (VCC)
+24V: J3.2, SW1.1 (A)
GND: D1.8 (GND), D2.8 (GND), D3.8 (GND), D4.8 (GND), J3.1, J7.39, J8.1, J9.1, J10.1, J11.1, J12.1, R2.2, U4.2 (in2), U4.4 (out2), U6.4 (GND)
unnamed: D1.2 (LPWM), J7.18
unnamed: D1.3 (R_EN), D1.4 (L_EN), J7.12
unnamed: D1.1 (RPWM), J7.16
unnamed: D2.2 (LPWM), J7.40
unnamed: D2.3 (R_EN), D2.4 (L_EN), J7.36
unnamed: D2.1 (RPWM), J7.38
unnamed: D3.2 (LPWM), J7.15
unnamed: D3.3 (R_EN), D3.4 (L_EN), J7.11
unnamed: D3.1 (RPWM), J7.13
unnamed: D4.2 (LPWM), J7.37
unnamed: D4.3 (R_EN), D4.4 (L_EN), J7.33
unnamed: D4.1 (RPWM), J7.35
unnamed: J2.1, J7.17
unnamed: J2.2, J7.19
unnamed: J2.3, J7.21
unnamed: J2.4, J7.23
unnamed: J2.5, J7.25
unnamed: J2.6, J7.27
unnamed: J2.7, J7.29
unnamed: J2.8, J7.31
unnamed: J6.1, J7.20
unnamed: J6.2, J7.22
unnamed: J6.3, J7.24
unnamed: J6.4, J7.26
unnamed: J6.5, J7.28
unnamed: J6.6, J7.30
unnamed: J6.7, J7.32
unnamed: J6.8, J7.34
unnamed: J7.3, U6.5 (AREF/PB0)
unnamed: J7.5, U6.7 (PB2)
unnamed: F1.1, J9.2
unnamed: J8.2, J10.2, J11.2, J12.2, SW2.2 (B)
unnamed: R1.1, SW1.2 (B), SW2.1 (A), U4.1 (in1)
unnamed: F1.2, U4.3 (out1)
unnamed: R1.2, R2.1, U6.2 (XTAL1/PB3)

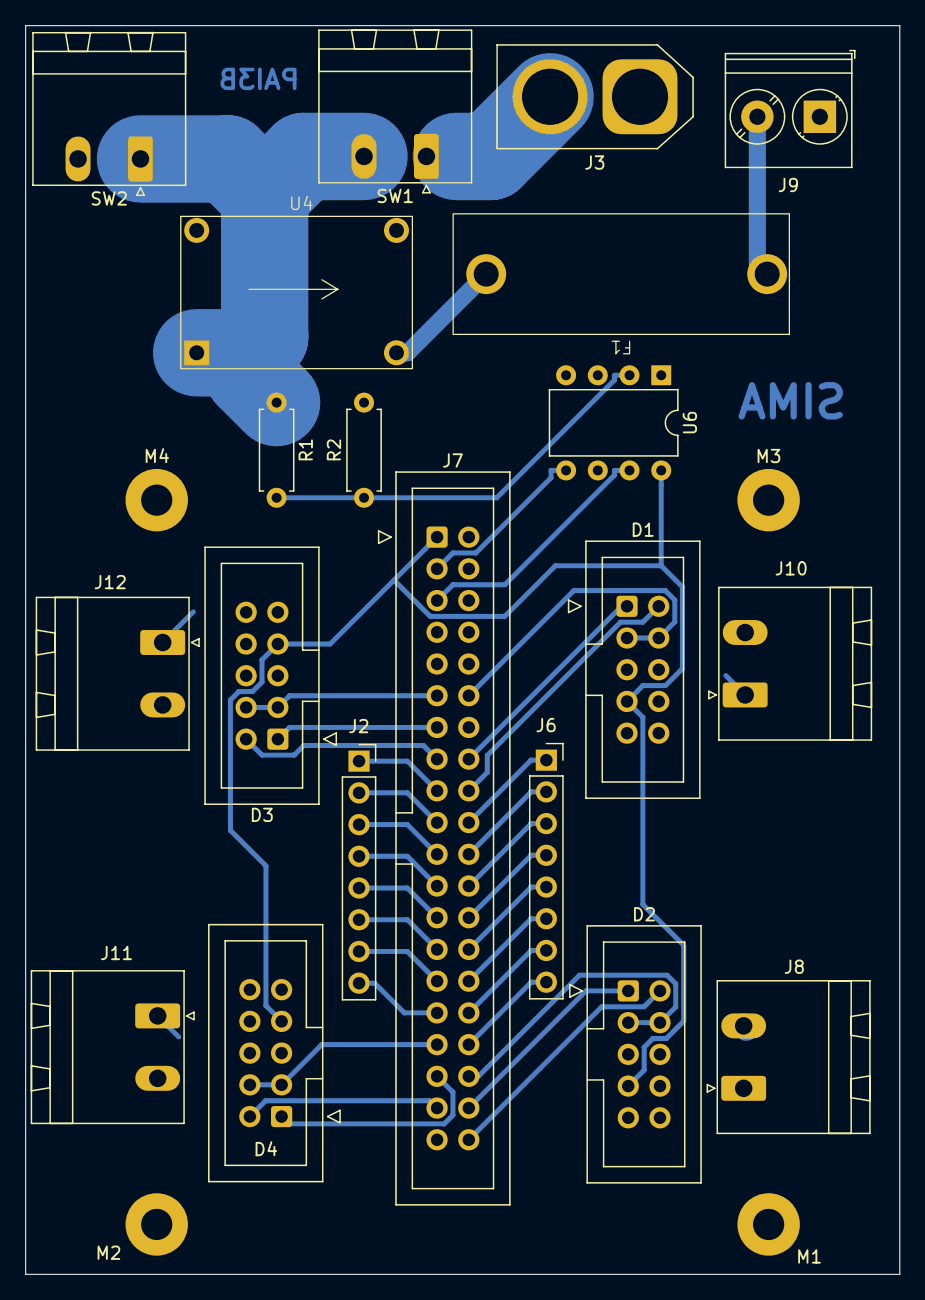
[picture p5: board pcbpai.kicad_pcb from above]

Board: 2 copper layers, 70.0 x 100.0 mm, 24 parts (0 on the bottom side), 38 nets.

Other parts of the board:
M1, M2, M3, M4: MountingHole_2.5mm_Pad

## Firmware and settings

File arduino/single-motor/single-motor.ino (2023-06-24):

/*
  Control a single motor using BTS7960

  This code is for controlling a single motor using BTS7960. The motor is a 24V DC motor with 16A max current (JCF63R-2480-160). The BTS7960 is a 43A H-Bridge motor driver.

  Hardware Required:
  - Arduino Board with 2 PWM pins
  - BTS7960
  - 24V DC motor
  - 24V power supply

  Connections:
  - Connect 24V power supply to BTS7960
  - Connect 24V DC motor to M+ and M- of BTS7960
  - Connect GND of Arduino to GND of BTS7960
  - Connect enable signals of BTS7960 to digital pins of Arduino
  - Connect PWM signals of BTS7960 to PWM pins of Arduino

  Libraries Required (unzip and copy to documents/Arduino/libraries):
  - BTS7960:
    https://github.com/luisllamasbinaburo/Arduino-BTS7960/

    Note: Change delay in BTS7960.hpp to 1000 us

  Created by Sebastian Dueñas
  Last updated on Jun/18/2023
*/

// PINOUT
// L_EN -> 8
// R_EN -> 8
// L_PWM -> 9
// R_PWM -> 10

#include "BTS7960.h"

const uint8_t L_EN = 13;
const uint8_t R_EN = 12;

const uint8_t L_PWM = 9;
const uint8_t R_PWM = 10;

// BTS7960::BTS7960(uint8_t L_EN, uint8_t R_EN, uint8_t L_PWM, uint8_t R_PWM)
BTS7960 motorController(L_EN, R_EN, L_PWM, R_PWM);

void setup()
{
  Serial.begin(9600);
}

void loop()
{
  motorController.Enable();
  Serial.println("Motor enable");

  motorController.TurnLeft(0);
  motorController.TurnRight(0);
  delay(2000);
  Serial.println("Turn off motor");

  Serial.println("Turn left (forward)");
  delay(3000);

  for (int speed = 80; speed < 100; speed += 5)
  {
    motorController.TurnLeft(speed);
    Serial.println("Speed up L " + String(speed));
    delay(2000);
  }

  Serial.println("Turn right (reverse)");
  delay(0);

  for (int speed = 80; speed < 100; speed += 5)
  {
    motorController.TurnRight(speed);
    Serial.println("Speed up R " + String(speed));
    delay(2000);
  }

  motorController.Disable();
  motorController.Stop();
  Serial.println("Motor disable");
}

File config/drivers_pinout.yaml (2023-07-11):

# GPIO pin number
driver_back_left:
  EN: 18 # GPIO 18, pin 12
  PWM_R: 23 # GPIO 23, pin 16 (Reverse)
  PWM_L: 24 # GPIO 24, pin 18 (Forward)

driver_front_left:
  EN: 16 # GPIO 16, pin 36
  PWM_R: 20 # GPIO 20, pin 38 (Reverse)
  PWM_L: 21 # GPIO 21, pin 40 (Forward)

driver_back_right:
  EN: 17 # GPIO 17, pin 11
  PWM_R: 27 # GPIO 27, pin 13 (Reverse)
  PWM_L: 22 # GPIO 22, pin 15 (Forward)

driver_front_right:
  EN: 13 # GPIO 13, pin 33
  PWM_R: 19 # GPIO 19, pin 35 (Reverse)
  PWM_L: 26 # GPIO 26, pin 37 (Forward)

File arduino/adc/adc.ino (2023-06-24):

/*
  Battery voltage measurement using ATtiny85 ADC

  This code is for measuring battery voltage using ATtiny85 ADC and sending
  the value to master device via i2c. The address of the slave device is
  0x08 and can be changed in the code.

  Hardware Required:
  - ATtiny85

  Connections:
  - Connect battery voltage to PB3 (ADC3)
  - Connect SDA to PB0
  - Connect SCL to PB2
  - Connect GND to GND
  - Connect VCC to VCC

  Note: ATtiny85 only can read voltages up to VCC, so if you want to
  measure voltages higher than 5V, you need to use a voltage divider.

  Libraries Required (unzip and copy to documents/Arduino/libraries):
  - TinyWire:
    https://github.com/lucullusTheOnly/TinyWire

  Programming:
  1. Set up Arduino IDE for ATtiny85:
    https://raw.githubusercontent.com/damellis/attiny/ide-1.6.x-boards-manager/package_damellis_attiny_index.json

  2. Upload ArduinoISP sketch to Arduino:
    File > Examples > ArduinoISP

  3. Set up Arduino IDE for ATtiny85:
    Tools > Board > ATtiny25/45/85
    Tools > Processor > ATtiny85
    Tools > Clock > 8 MHz (internal)
    Tools > Programmer > Arduino as ISP

  4. Connect Arduino to ATtiny85:
    Arduino 5V > ATtiny85 VCC
    Arduino GND > ATtiny85 GND
    Arduino 10 > ATtiny85 Reset
    Arduino 11 > ATtiny85 PB0
    Arduino 12 > ATtiny85 PB1
    Arduino 13 > ATtiny85 PB2

  5. Upload code to ATtiny85

  Created by Cristian Chitiva (cychitivav@unal.edu.co)
  Last updated on Jun/5/2023
*/

#include <TinyWire.h>
#define ADDR 0x08

void setup()
{
  pinMode(3, INPUT);               // Set PB3 (ADC3) as input
  TinyWire.begin(ADDR);            // config TinyWire library for I2C slave functionality
  TinyWire.onRequest(sendVoltage); // register a handler function in case of a request from a master
}

void loop()
{
}

void sendVoltage() // this function is called when the master requests data
{
  int voltage = analogRead(3); // Read voltage from PB3 (ADC3)

  TinyWire.send(voltage >> 8);   // Send high byte
  TinyWire.send(voltage & 0xFF); // Send low byte
}

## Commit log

2023-05-02 add kinematics damping system calculations implementation of the inverse kinematics of the damping system to find the position of the linkages and calculate the force of produce by the damper station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
2023-05-16 motor calculations in two methods
2023-05-16 motor calculations simplified
2023-05-16 add content to wheel notebook
2023-05-31 Dev/ros package (#24)
    * Added ros package & robot urdf description
    * add wheel mesh
    * modify urdf
    * add center mesh
    * Added meshes & measures for urdf description
    * update docker image to ros noetic
    * add instructions of running to REAADME
    * fix Dockerfile
    * docs: update ROS version in documentantion
    - Reflect change from ROS 2 to ROS 1 in the documentation
    - Specify ROS noetic is being use in the development of the package
    - Set license parameter in ROS package
    ---------
    [robot_view.urdf]
2023-06-05 Dev/kinematic model (#25)
    * modify urdf with xacro macro
    * add simulation launch
    * add rqt dependencies
    * fix left wheels
    * add hardware interface
    * remove view_robot.urdf after merge
    * fix wording
    * fix Jacobian definition
    * change docker base image
    * add max velocity parameter
    - define a linear and angular velocity limit
    * add comments with reference of the math used
    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
    [controller.yaml, robot.urdf, robot_view.urdf]
2023-06-06 Dev/motor drivers (#26)
    * [FEAT]: add driver library
    * docs: raspberry pin out
    * break experomental
    * remove submodule
    * [FEAT]: add library
    * add setup
    * [FIX]: driver lib and docker file
    - driver lib variable typo
    - docker file clean unnecessary configurations
    * [FEAT]: driver node
    - create driver node subscriber
    - document raspberry set up process
    * [REFACT]: motor_driver subs
    - split call_back for indivual motor velocity message
    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
    [motor_driver.py]
2023-06-07 Dev/battery sensor (#27)
    * add attiny reader
    * finish arduino program for attiny85
    * add battery node
    * add battery script to cmakelists
    * fix import
    * fix import std_msgs
    * custom service
    * fix srv data
    * fix battery constants
    * fix power battery names
    * fix serial number
    * refactor attiny name
    * fix BatteryState msg
    * add rospy logs
    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
    [adc.ino, battery.py]
2023-06-07 Fix/driver lib remote (#29)
    * remove lib from motor_driver.py
    * remove lib instance and add pigpiod remote
    * add pigpiod to Dockerfile for use outside raspi
    * remove lib submodule
    * remove gitmodule
    * install `pigpiod` from pip
    * [FEAT]: driver with no arguments
    - configure driver to run with no arguments.
    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
    [drivers_pinout.yaml, motor_driver.py]
2023-06-08 change PWM to software
2023-06-09 update pins to handle PWM through software and hardware
2023-06-10 [FIX]: joint names in controller parameters (#32)
    [controller.yaml]
2023-06-14 [FEAT]: ramp and pwm change direction protection (#39)
    * speed slow change
    * fix negative change
    * change frequency to 160Hz
    * add signal shutdown detection
    * add on shutdown callback
    * [FEAT]: separate ramp into independent function
    - create change of direction protection feature
    - remove ramp behavior from set_speed into a independent function
    Co-authored-by: Sebastian <jsduenass@unal.edu.co>
    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
    [motor_driver.py]
2023-06-14 Revert "[FEAT]: ramp and pwm change direction protection (#39)" (#41)
    This reverts commit 48275a6a935ebef47f731a84f05b0457bfe6c0cc.
    [motor_driver.py]
2023-06-24 testing motor driver BTS7960 (#45)
    * [FEAT]: single motor testing new BTS7960 drivers
    * [FEAT]: adding multiple motors
    * comment single motor arduino
    * add control from an arduino mega and BTS7960 library
    * modify pins new drivers (BTS7960)
    * change logic for BTS7960 driver
    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
2023-06-24 Dev/pcb (#44)
    * remove backup and cache files
    * remove extra README files
    * add backup folders to gitignore
    * add footprints
    * refactor kicad folder
    * add 3d models and footprints to kicad
    * center raspberry mounting holes
    * update libraries and change trace width
    * add fuse 3d model
    * add terminal blocks for sensors and 24+ zone
    * fix regulator model
    * finish pcb
    * add gerber files and change footprints
    * fix XT60 polarity
    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
    [Fuse Holder.step, dsn-mini-360.step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]
2023-07-05 Update driver pins
2023-07-05 Add i2c setup to docs
2023-07-05 fix sys argv length
    [battery.py, motor_driver.py]
2023-07-05 fix battery detect i2c attiny
    [battery.py]
2023-07-05 Replace sys.argv with rospy.myargv
    [battery.py, motor_driver.py]
2023-07-13 Fix simulation and comment velocity limits in kinematic model (#49)
    [robot.urdf]
2023-07-13 Fix/dev container display (#52)
    * Fix simulation and comment velocity limits in kinematic model
    * Clean devcontainer
    * Add workspace folder
    * Fix workspace folder
    * Change workspace mount and source catkin build
    * Add ssh to devcontainer
    * Remove env from dockerfile
    * Fix tipo '_wheel' and add xauth to devcontainer
    * Add git to devcontainer
    * Remove passwd from devcontainer.json
    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
    [controller.yaml]
2023-07-13 docs review readme (#50)
    * Add badges for kicad and raspberry
    * add authors
    * Document Codespace configuration in README
    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
